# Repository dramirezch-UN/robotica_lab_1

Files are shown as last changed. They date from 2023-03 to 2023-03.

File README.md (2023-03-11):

# Robótica Laboratorio 1

## Herramienta

El diseño de la herramienta se basó en el datasheet de robot ABB IRB140, desde el cual se consiguieron las dimensiones de la placa de montaje para poder transportarlas al diseño en Inventor.
plano_datasheet

El objetivo principal en el diseño de la herramienta fue asegurar que el eje z del plano de montaje y el eje z de la herramienta no estuvieran alienados. Para poder evitar problemas de singularidad en futuros laboratorios. También se tuvo en cuenta las limitaciones de la fabricación por impresión 3D. Por lo cual, se imprimió de manera modular para ensamblar las piezas como la herramienta final.

inventor

Se utilizó un tubo de PVC de 1/2 para recibir el marcador, aunque debido a un error por no tener en cuenta las tolerancias de fabricación se tuvo que cortar en la parte inferior para poderlo insertar. Se usó un resorte compensar la curvatura e imperfecciones del tablero.

A partir de este diseño se realizó una versión que simula el tubo de PVC junto con el marcador dentro de este para poder tener un modelo fidedigno con el cual trabajar en Robot Studio.

inventor_herramienta_final

Tras imprimir las piezas diseñadas y comprar los demás materiales, se ensambló la herramienta que sostiene al marcador. Se realizaron unos pequeños ajustes para facilitar su uso:

1. Al tener la herramienta ensamblada nos dimos cuenta de que era probable que el marcador se saliera de su sitio, ya que no estaba amarrado al tubo de PVC. Por esto, el primer ajuste que se hizo fue agregar cinta que conectara al marcador con el tubo de tal forma que no fuera posible que el marcador se saliera, pero que la cinta permitiera el movimiento del marcador hacia adentro del tubo.
2. Nos dimos cuenta de que los agujeros para los tornillos M6 eran muy pequeños. Por esto, tuvimos que ampliarlos. 

herramienta

Con estas modificaciones, la herramienta pudo ser montada en el robot sin más complicaciones.

herramienta_calibracion

Para calibrar la herramienta en el robot, se realizó el proceso de llevarlo a un punto 3 veces desde posiciones iniciales distintas.

herramienta_guardada

## Programación en Robot Studio
El primer paso a seguir, una vez calibrada la herramienta, fue la de realizar la programación en Robot Studio de la rutina a seguir por el IRB 140. 

Lo primero, fue exportar la herramienta modelada en Inventor a Robot Studio, donde gracias a este procedimiento, fue mucho más fácil la definición del TCP y su precisión a la hora de escribir en la realidad.

Herramienta en simulador

Una vez realizada la respectiva configuración de la herramienta con su alineación, se procedió a exportar las guía para definir los puntos de las letras y poder programar las trayectorias. Como con la herramienta, las letras se diseñaron en Inventor y se exporta a Robot Studio como un objeto. Con el objeto exportado, se le ubicó a una distancia apta para que el brazo alcanzara a llegar sin problema. Se ubicó a x=500 y=100 z=0. 

Con la ubicación definida, se procedió a establecer los puntos en las letras para programar las trayectorias. En donde existen curvas, se marcaban 3 puntos para definir dos trayectorias y que se pudiese generar la curva deseada. Para las trayectorias rectas solo se definían dos puntos. También fue necesario generar puntos para llevar al robot desde el home hasta las letras, para así evitar que 2 o más articulaciones quedaran lineales una respecto a la otra. También fue necesario establecer puntos por encima del plano de escritura para levantar que el brazo hiciera un trazo continuo entre letra y letra. Es de aclarar que todos los puntos deben de invertirse para que la herramienta pueda "atacarlos" correctamente.

Trayectoria externa de la O

Con ello definido, se crearon un total de 7 Paths como trayectorias, donde cada dos Paths representarían a una letra, sin contar el primero, que se considera como el acercamiento inicial. Con esto configurado, se procedió a realizar pruebas en el simulador, donde se obtuvieron resultados satisfactorios.

Foto del simulador en uso

Por último, se realizó la validación en otra posición desplazando el workobject, arrojando resultados satisfactorios. Se realiza la exportación a RAPID y se lleva al laboratorio.

## Programa
Teniendo el código en Rapid listo para ser usado, se cargó este código al robot y se realizó una primera prueba sin montar la herramienta.

En este punto nos dimos cuenta de que faltaba una instrucción al final del programa, la de volver al home. Por lo que se editó el código en RAPID desde el flex pendant para agregar esto.

Se volvió a ejecutar el programa sin la herramienta y tras verificar que el resultado obtenido era el esperado, se montó la herramienta y se realizó una segunda prueba. Para esta prueba, se tomó la precaución de que la herramienta no tocara el tablero. Esto se consiguió cambiando la ubicación z del work object.

Tras esto, se empezó a bajar la ubicación en z del work object hasta que la herramienta tocara el tablero. Desafortunadamente, la ubicación escogida en el tablero no era plana.

robot_2_mal

Por esto, se realizó el mismo proceso en el otro robot y se obtuvieron los resultados esperados:

ubicacion_1

Luego, para cumplir el requisito de escribir en otra ubicación, se cambiaron las coordenadas del work object y se volvió a correr el programa.

ubicacion_2

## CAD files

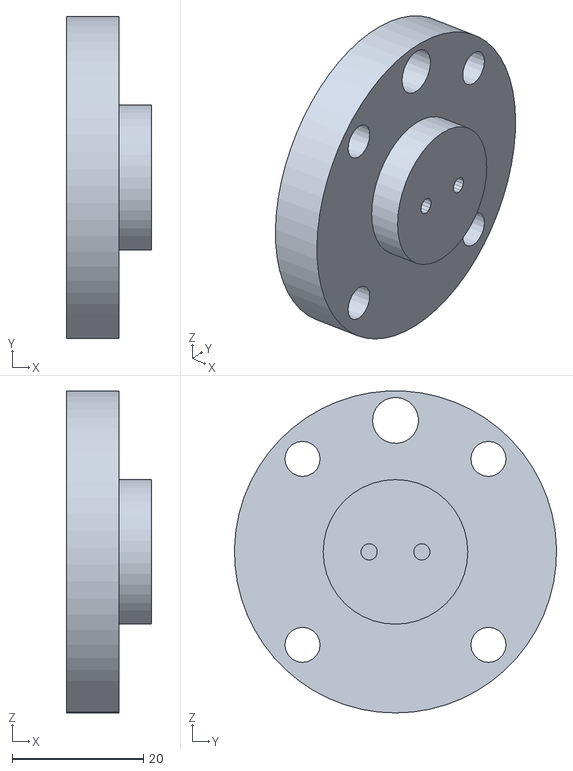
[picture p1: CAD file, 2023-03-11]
diseno_herramienta/inventor/Herramienta Marcador Base.stl
13.0 x 49.0 x 49.0

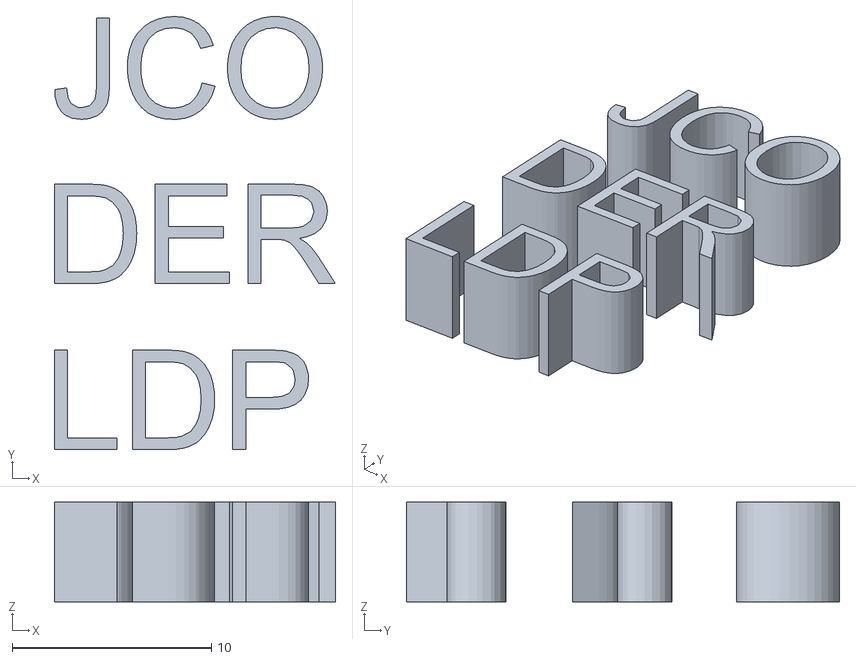
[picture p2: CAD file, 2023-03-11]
iniciales/Iniciales.stl
14.1 x 21.8 x 5.00

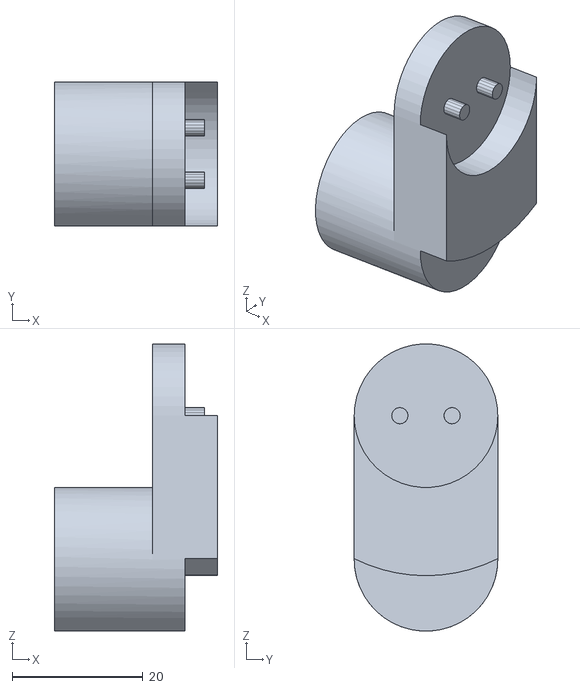
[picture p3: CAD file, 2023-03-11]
diseno_herramienta/inventor/Herramienta Marcador Conector.stl
25.0 x 22.0 x 43.9

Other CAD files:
diseno_herramienta/inventor/Herramienta Marcador Base.ipt
diseno_herramienta/inventor/Herramienta Marcador Conector.ipt
diseno_herramienta/inventor/Herramienta Marcador.iam
diseno_herramienta/inventor/Marcador.ipt
diseno_herramienta/inventor/OldVersions/Herramienta Marcador Base.0005.ipt
diseno_herramienta/inventor/OldVersions/Herramienta Marcador Conector.0012.ipt
diseno_herramienta/inventor/OldVersions/Herramienta Marcador Tubo.0006.ipt
diseno_herramienta/inventor/OldVersions/Herramienta Marcador.0001.ipt
diseno_herramienta/inventor/OldVersions/Herramienta Marcador.0012.iam
diseno_herramienta/inventor/OldVersions/Marcador.0001.ipt
iniciales/Iniciales.dwg
